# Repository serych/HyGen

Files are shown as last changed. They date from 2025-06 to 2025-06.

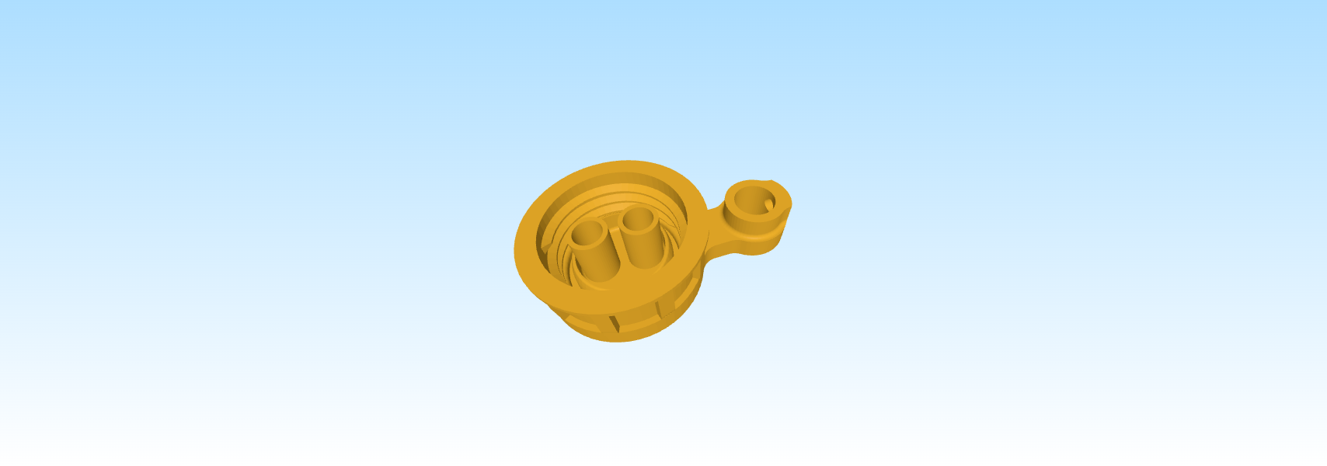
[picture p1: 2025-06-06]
images/ImageToStl.com_Bottle-cap-2tubes.png

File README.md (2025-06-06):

# HyGen
Construction of cheap hydrogen generator using GT-A060 PEM electrolytic cell.

## Material needed 
- GT-A060 PEM electrolytic cell (AliExpress around $35)
- 300W 20A DC-DC Buck Converter Step Down Module Constant Current (AliExpress around $5)
- Digital Voltmeter DC 100V 10A Voltmeter Ammeter Blue + Red LED (AliExpress around @3)
- Power supply with voltage 5 to 30 V and power around 50 W (I use 19 V supply from old notebook)
- 6 mm (1/4") tubes 3 - 4 meters 
- 8 mm (1/3") aluminium rod or tube 55 cm long
- printed parts
- 0.5 l Coca-Cola bottle
- PET bottle preforms (40ml Plastic Test Tubes with Metal Screw Cap on AliExpress) - 2 PCs
- Reusable Silica Gel desiccant (ideal is the blue type which changes color when moistened) 
- piece of nylon stocking or similar fabric and two small elastic bands or pieces of wire
- screws M3/20mm 4 PCs with brass heatstake inserts, screws M3/12mm with nuts 2 PCs, screws M5/15mm 2 PCs

## Printed parts
- stand with holders for PEM cell, converter, and voltmeter/ammeter
- bottle cap - 4 tubes for water container from a Coca-Cola bottle
- bottle cap - 3 tubes for hydrogen/water separator
- bottle cap - 2 tubes for silica gel desiccator

## Workflow
- 3D print the parts (don't forget to add supports to the 4 bottom holes on the stand in slicer)
- seal inserts to the bottle caps and rod holder on the stand and insert M3 srews
- thread the tubes through the holes in the caps according to the diagram (I found it helpful to cut the tubes diagonally first to make them easier to insert into the holes)
- attach strainers made from pieces of nylon stockings to the ends of the tubes in the desiccator using rubber bands or wire to prevent the silica gel from falling into the tubes
- attach the PEM cell and converter to the stand using the screws
- connect the electric circuit according to the diagram
- insert the correct ends of the tubes into the quick connectors on the PEM cell according to the diagram
- fill the desiccator bottle with silica gel (the longer tube must be first inserted deep into bottle)

## First hydrogen generator adjustment

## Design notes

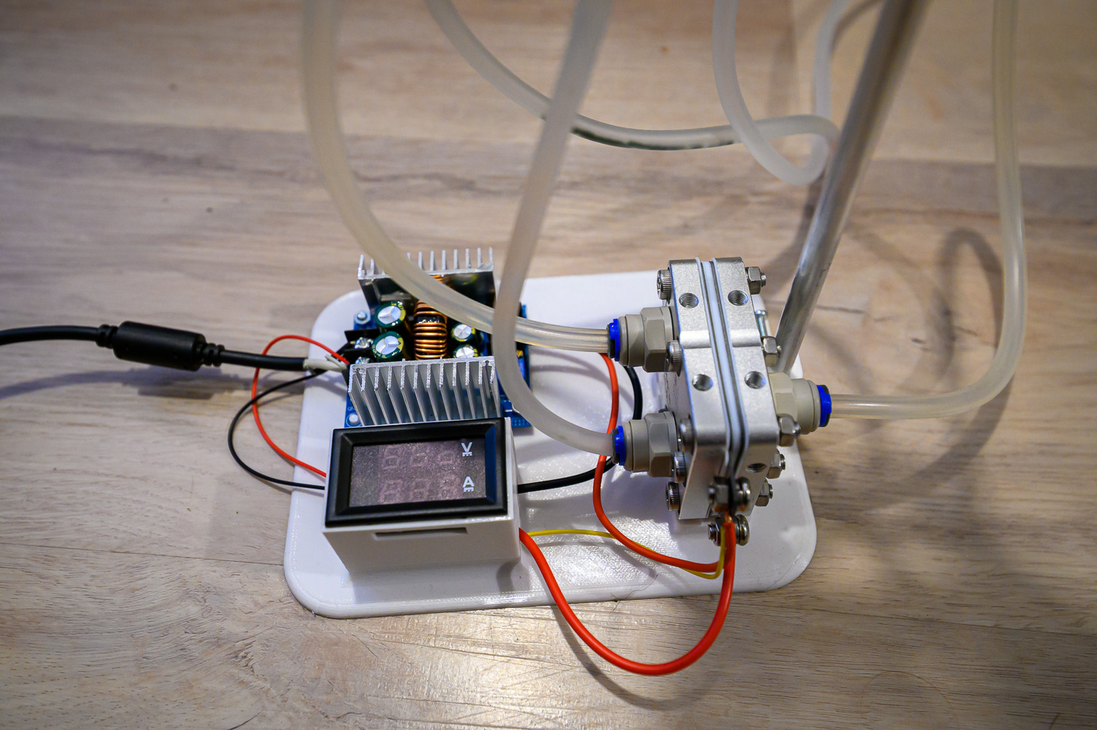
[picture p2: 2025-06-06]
images/25-06-06.JaSe.JS7_3626.jpg

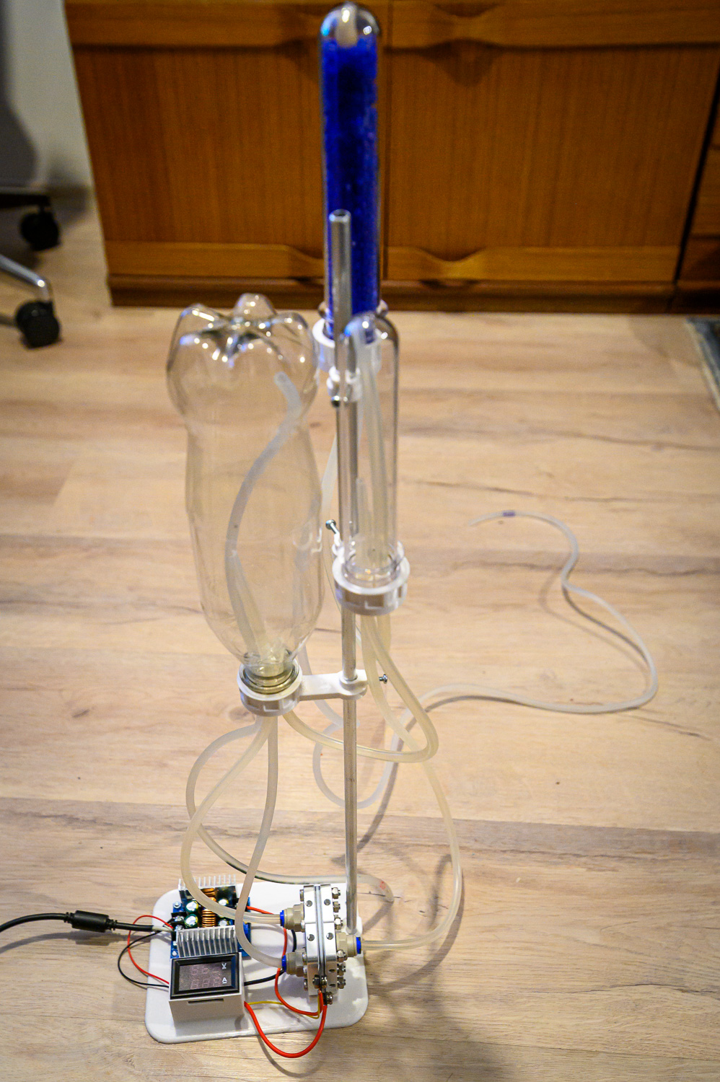
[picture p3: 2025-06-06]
images/25-06-06.JaSe.JS7_3625.jpg

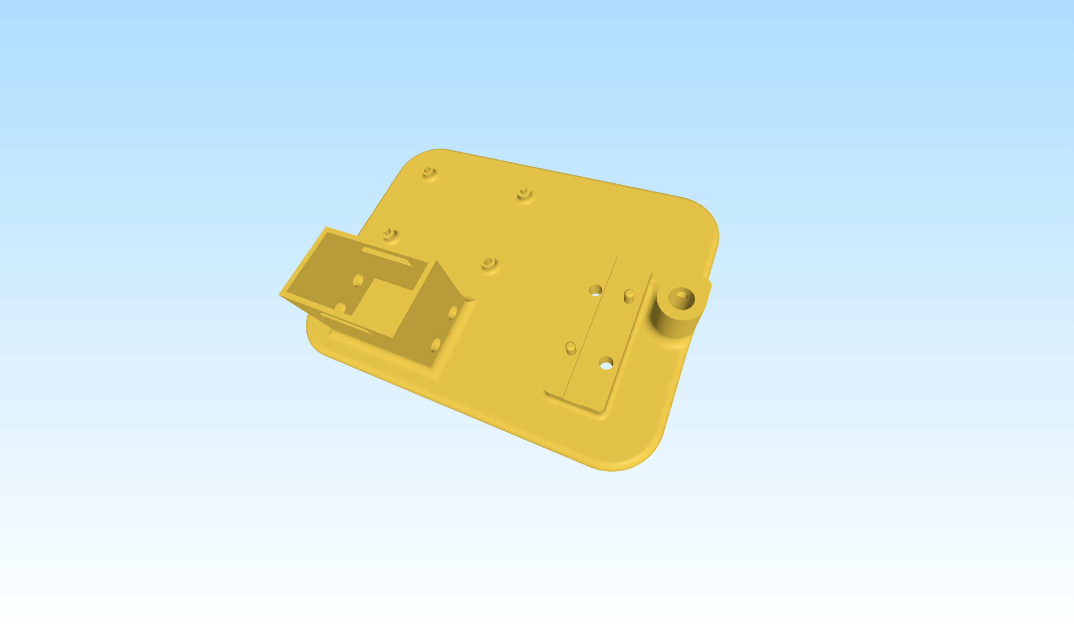
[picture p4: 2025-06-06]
images/ImageToStl.com_Hydrogen_generator.png

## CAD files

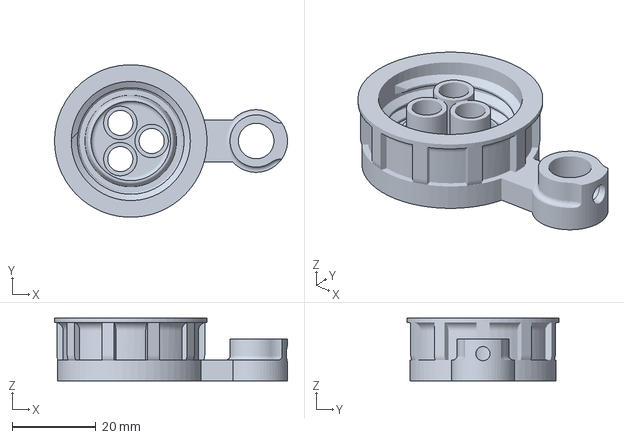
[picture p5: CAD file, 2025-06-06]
3D printed parts/3MF format/Bottle-cap-3tubes.3mf
55.8 x 36.4 x 15.0 mm

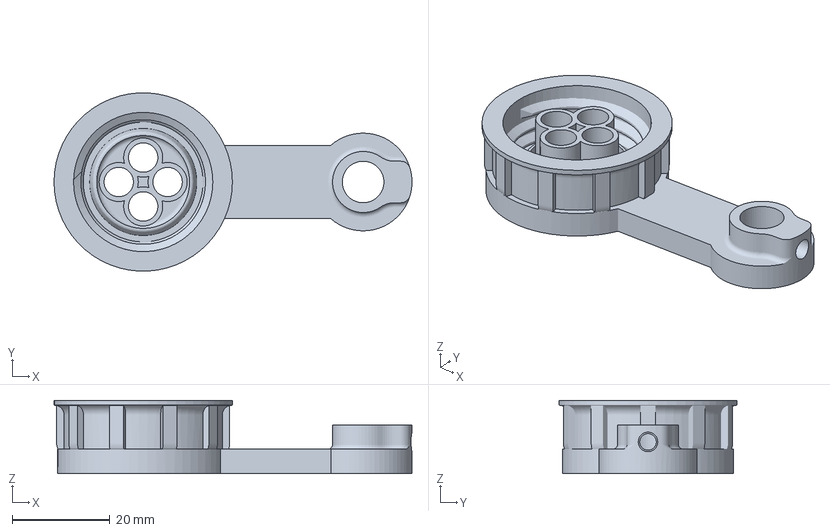
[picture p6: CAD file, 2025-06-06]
3D printed parts/3MF format/Bottle-cap-4tubes.3mf
73.2 x 36.4 x 15.0 mm

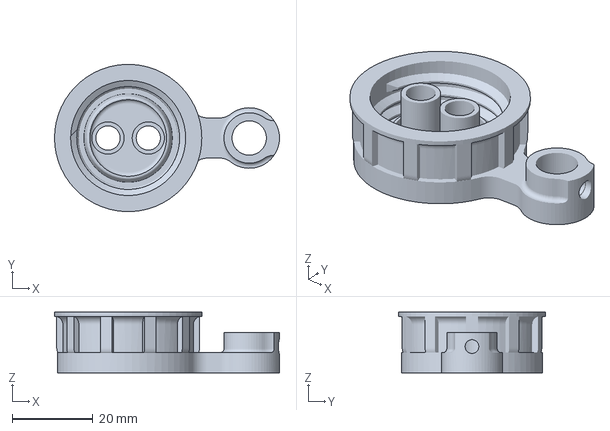
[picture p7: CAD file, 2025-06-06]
3D printed parts/3MF format/Bottle-cap-2tubes.3mf
55.8 x 36.4 x 15.0 mm

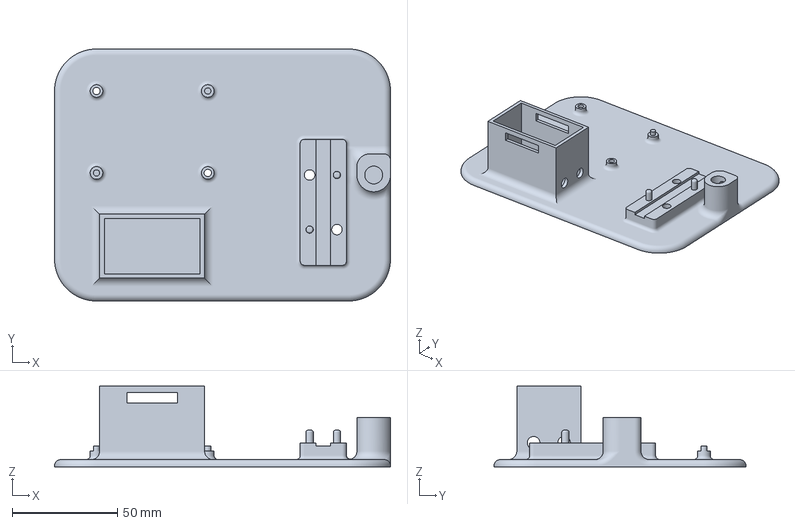
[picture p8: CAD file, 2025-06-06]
3D printed parts/3MF format/Hydrogen_generator.3mf
160.0 x 120.0 x 38.5 mm
